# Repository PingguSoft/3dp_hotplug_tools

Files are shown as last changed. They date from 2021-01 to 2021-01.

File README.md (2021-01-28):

# [ 3dp_hotplug_tools](https://github.com/PingguSoft/3dp_hotplug_tools)

## hot-pluggable 3d printer tools
 - remixed from ProperPrinting's tools 
 - https://www.thingiverse.com/thing:3369444
 - https://www.thingiverse.com/thing:3547740
 - female connector is built in the base and male connector is built in the tools
   - **big current flows through VBB (24V for ender3) and extruder heater pins, so 4 pins for each are assigned**
   - **required voltages can be driven through VBB and GND by using DC-DC converter**
 
## base
 - female connector is installed by 15 degree angle 

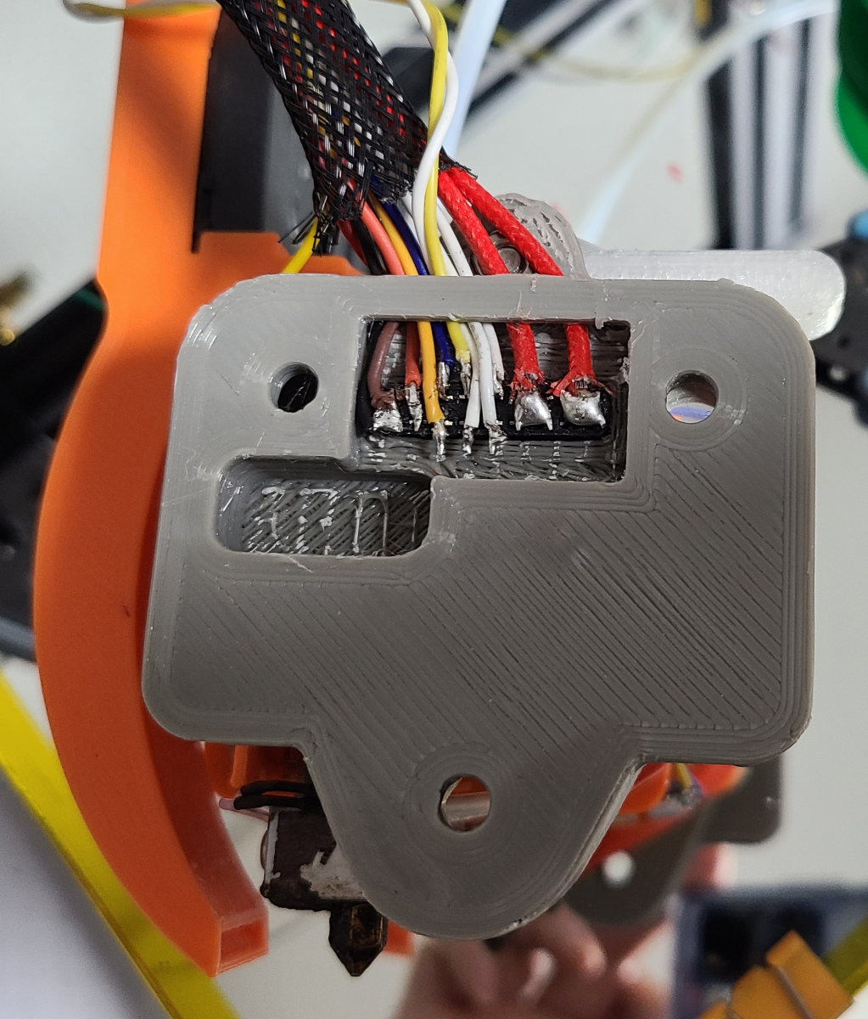
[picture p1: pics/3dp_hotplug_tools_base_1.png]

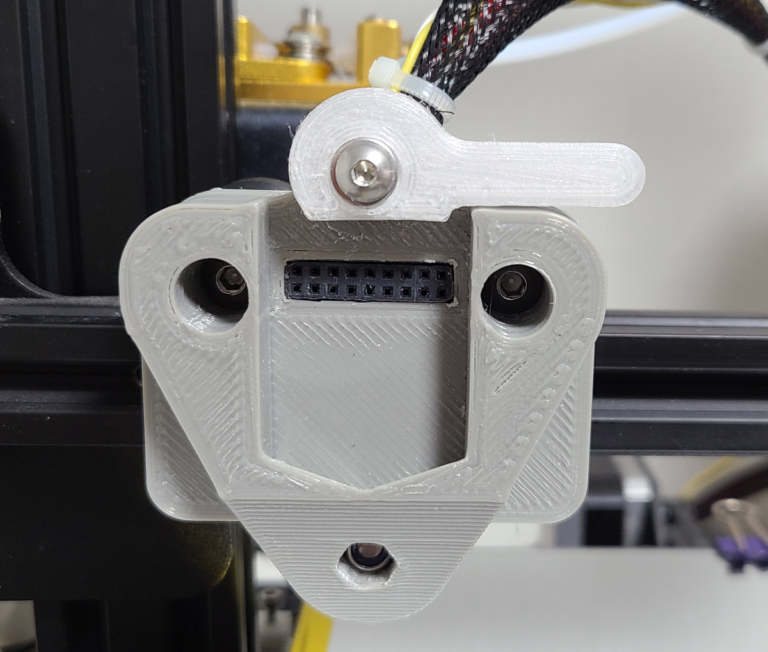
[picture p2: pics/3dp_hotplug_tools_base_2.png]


## head tool pin connection
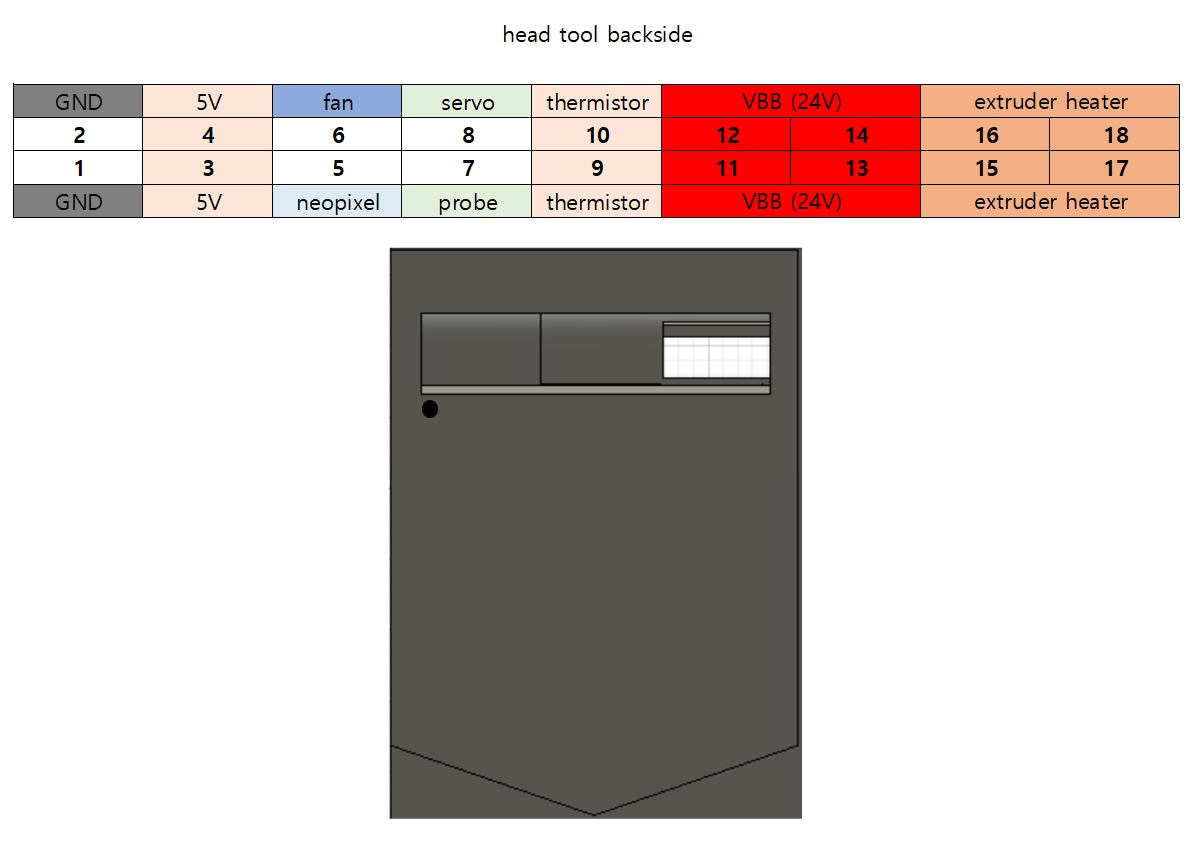
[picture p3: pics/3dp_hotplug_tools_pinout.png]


## 3dp hotend tool
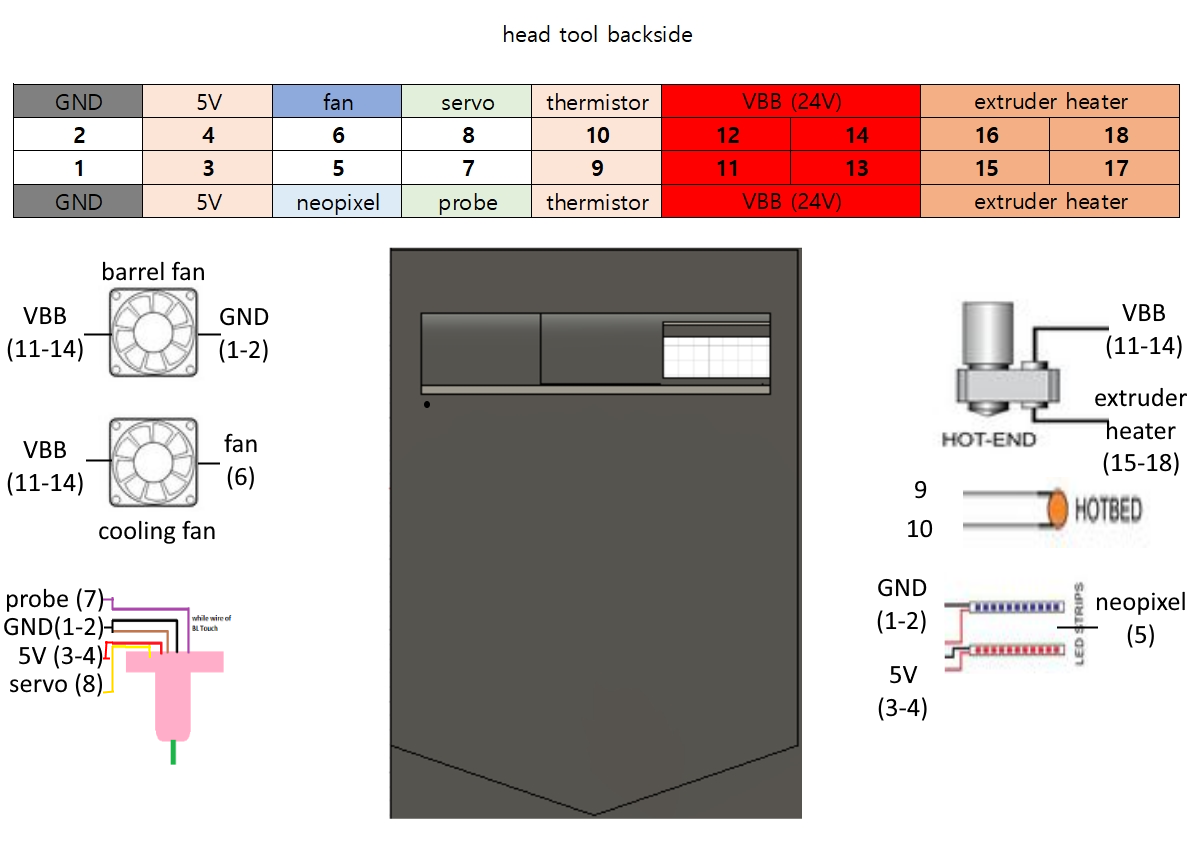
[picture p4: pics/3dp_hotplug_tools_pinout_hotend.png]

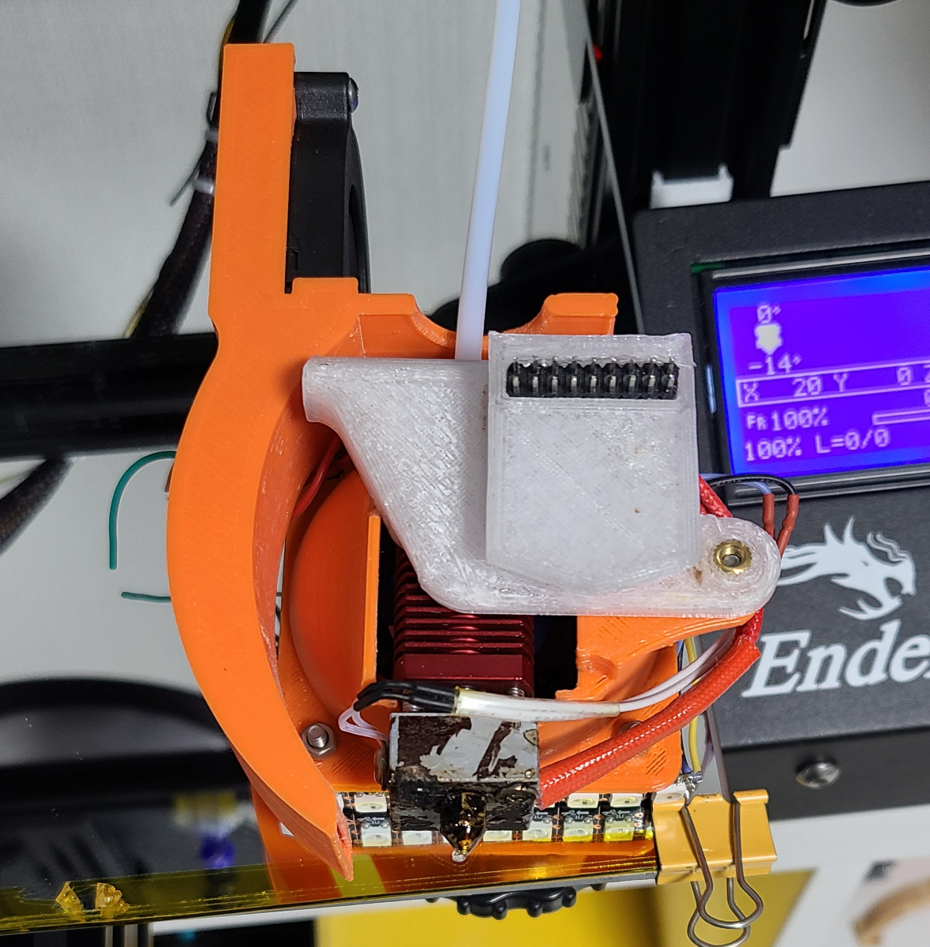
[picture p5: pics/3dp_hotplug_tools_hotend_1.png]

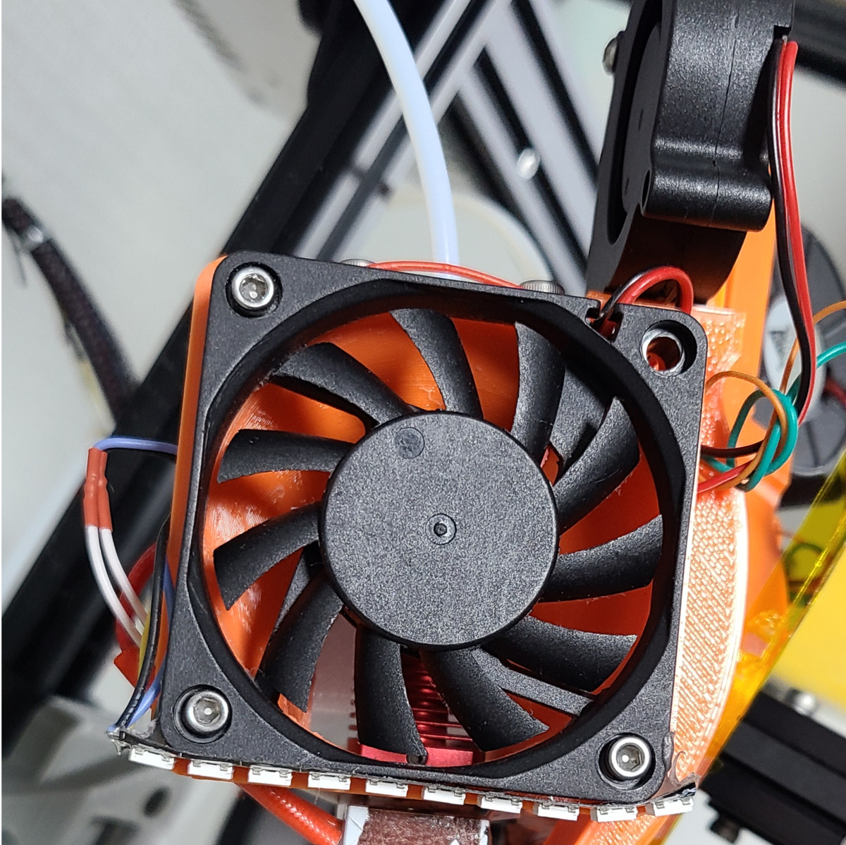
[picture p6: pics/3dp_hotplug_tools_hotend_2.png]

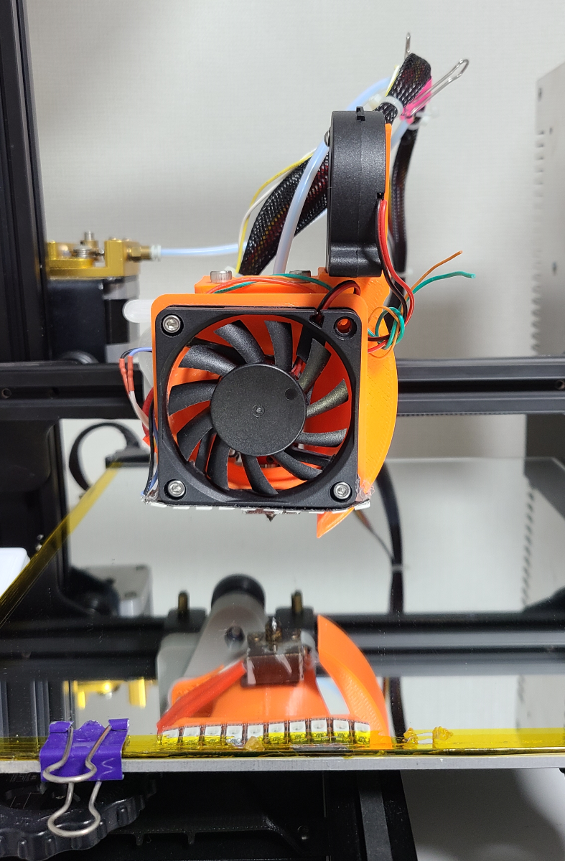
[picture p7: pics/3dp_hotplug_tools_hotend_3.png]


## plotter tool
 - pen is moved up and down by using fan signal to speed up
 - pen is moved by solenoid and gravity and move up when solenoid is on (=fan is on)
 - cura plugin for the plotter is [here](https://github.com/PingguSoft/cura_plugin)
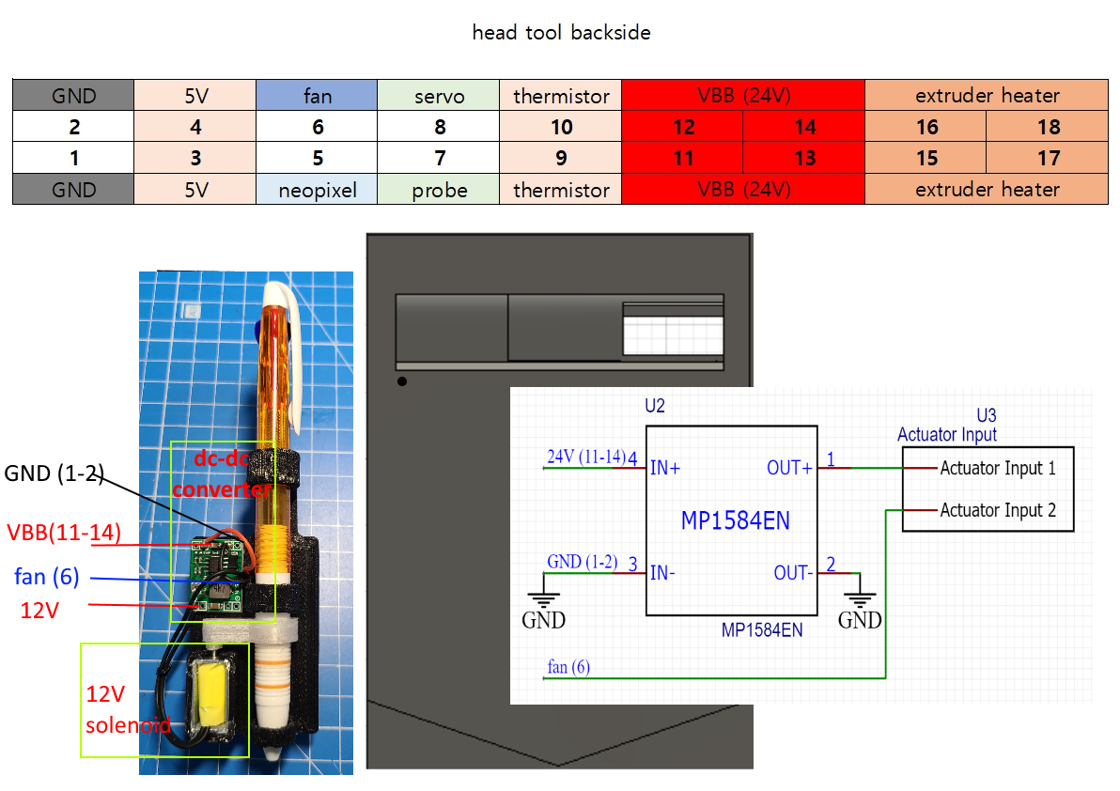
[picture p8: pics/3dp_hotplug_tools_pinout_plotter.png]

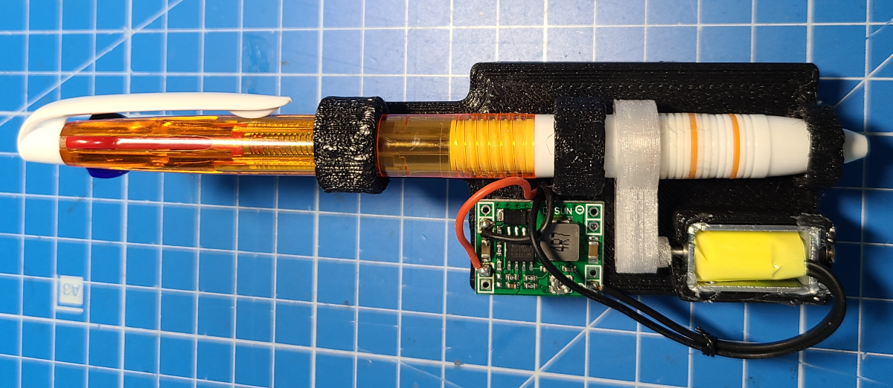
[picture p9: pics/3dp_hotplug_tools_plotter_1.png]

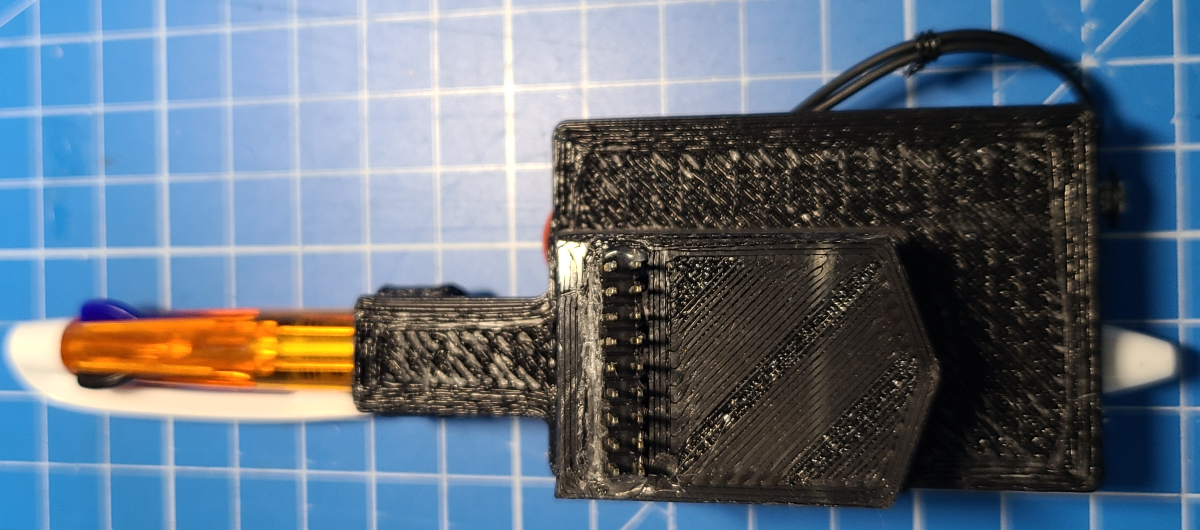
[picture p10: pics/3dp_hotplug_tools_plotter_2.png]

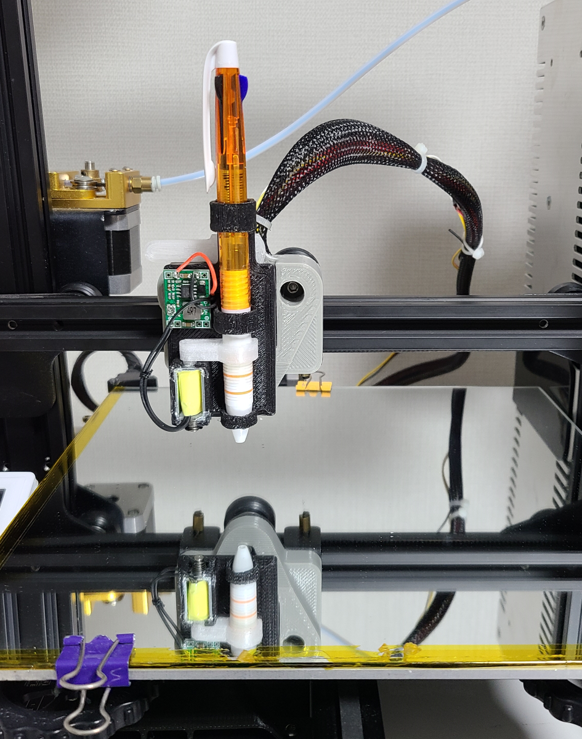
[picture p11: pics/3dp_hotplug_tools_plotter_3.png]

<div >
  <a href="https://www.youtube.com/watch?v=ooa_5NmSuvM">
</div>

## laser tool
 - laser voltage is controlled by using fan signal for laser module without pwm signal
 - if laser module has pwm signal, 15A mosfet module is not required
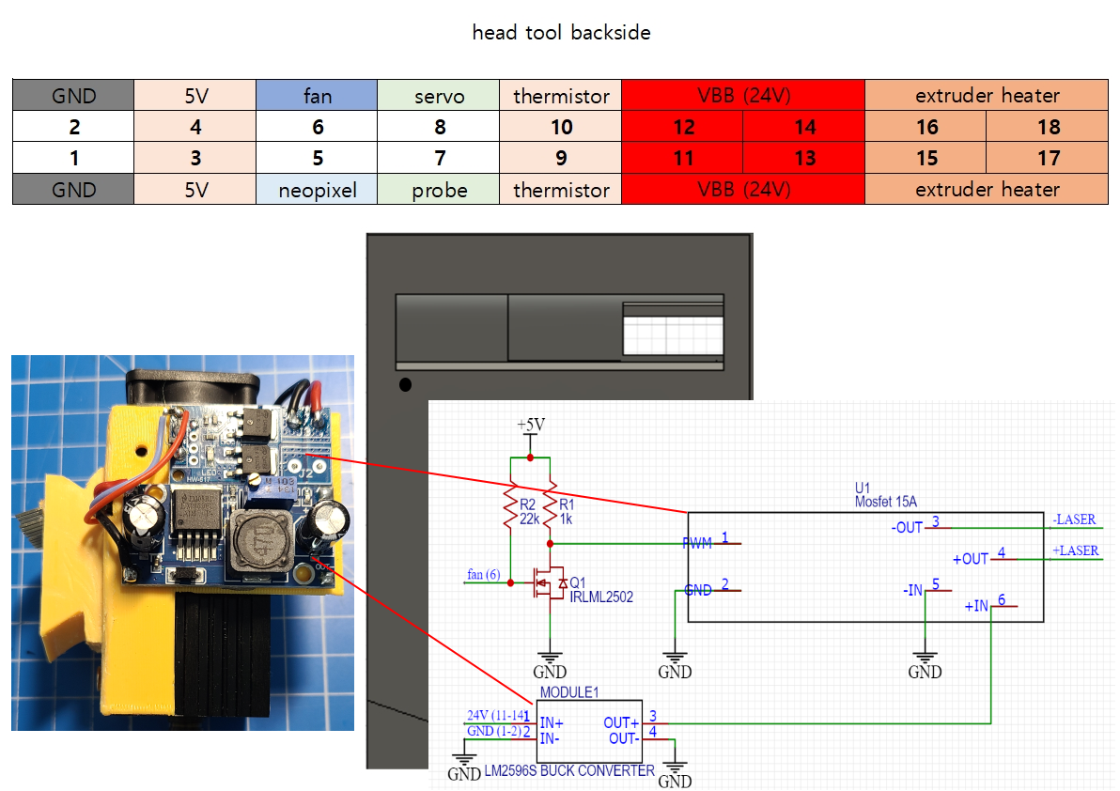
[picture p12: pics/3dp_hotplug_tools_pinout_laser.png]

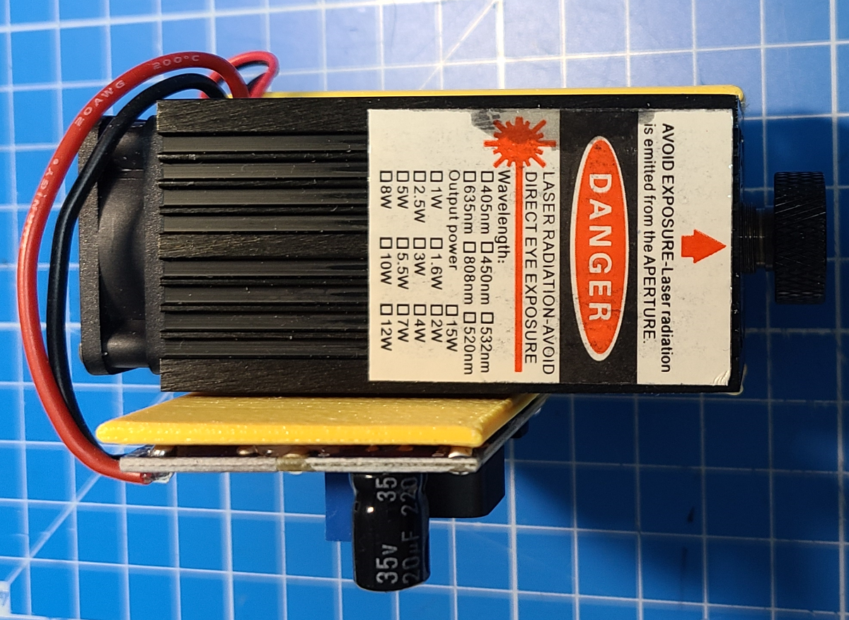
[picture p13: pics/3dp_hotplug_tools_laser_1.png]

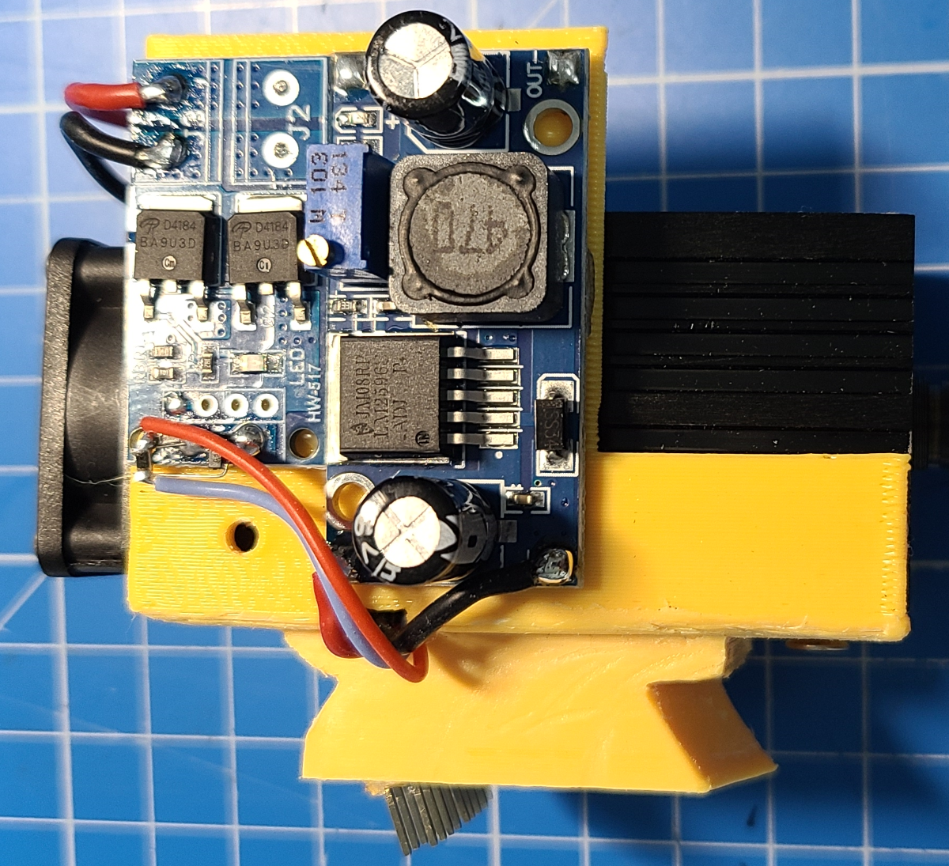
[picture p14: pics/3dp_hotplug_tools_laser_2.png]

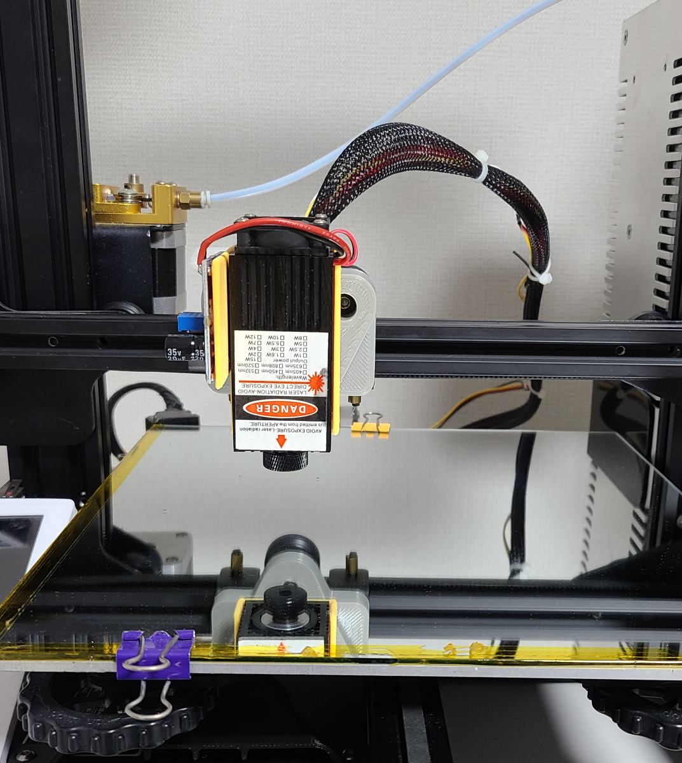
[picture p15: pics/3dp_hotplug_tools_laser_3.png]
<div>
 <a href="https://www.youtube.com/watch?v=72gGR1SVQI4">
</div>

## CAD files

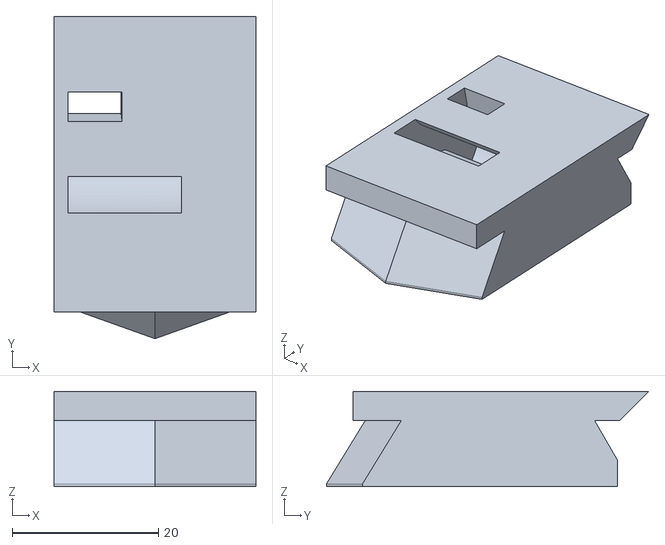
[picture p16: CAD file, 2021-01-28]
stl/06.tools-template.stl
27.6 x 44.1 x 13.0

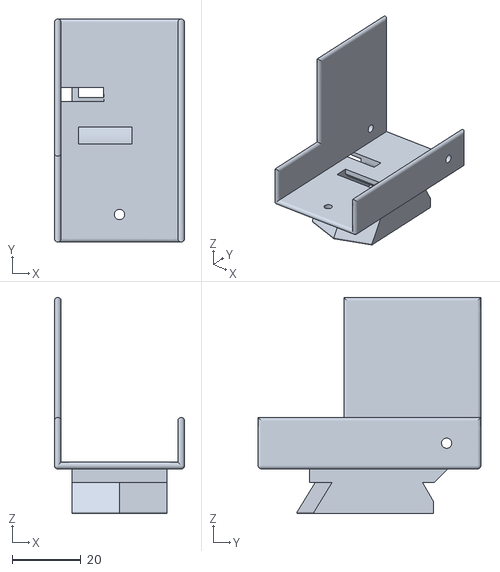
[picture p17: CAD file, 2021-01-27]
stl/05.laser.stl
38.0 x 65.0 x 63.0

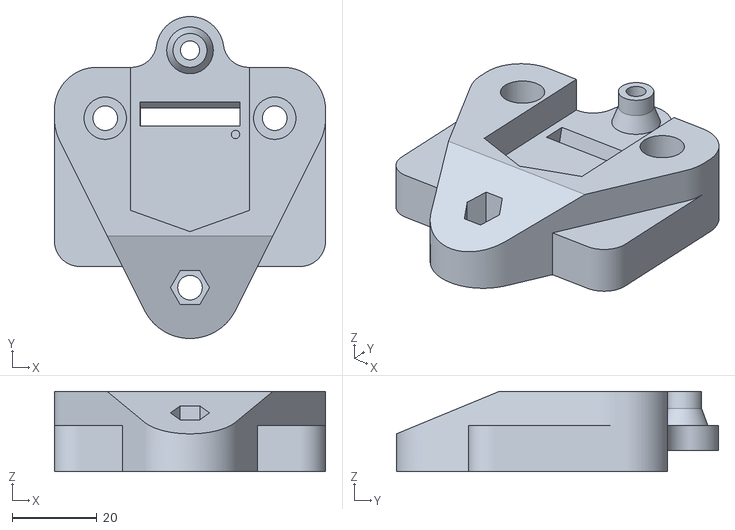
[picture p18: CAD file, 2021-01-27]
stl/01.base.stl
64.0 x 76.0 x 18.9

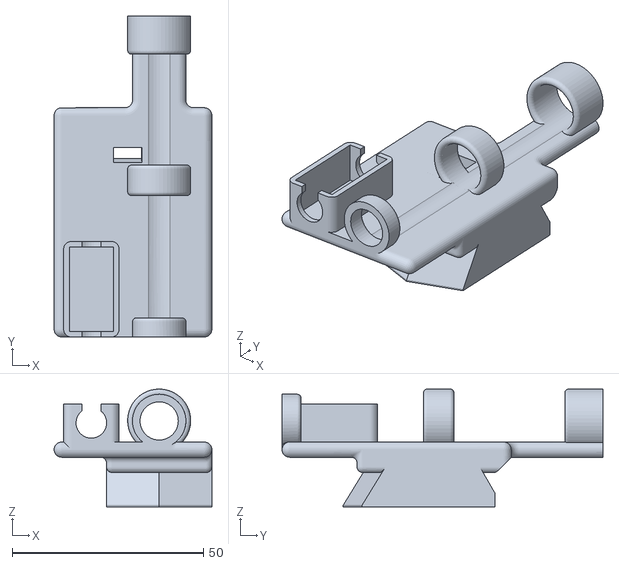
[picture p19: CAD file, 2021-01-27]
stl/03.pen_head.stl
41.3 x 84.0 x 30.9

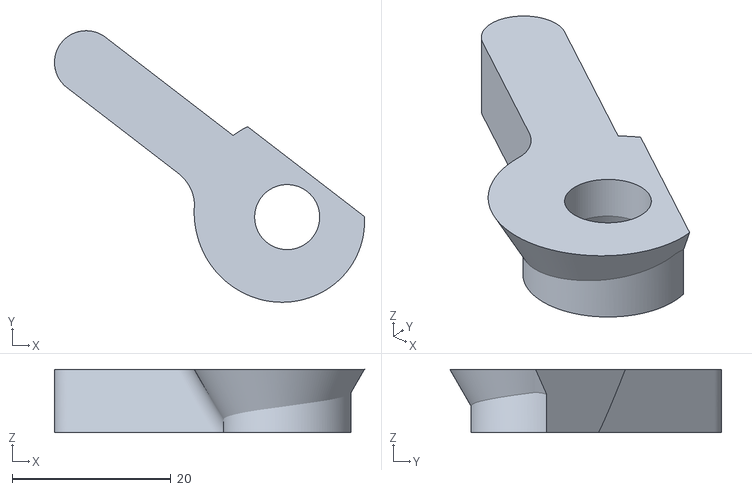
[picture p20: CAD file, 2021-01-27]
stl/06.V2_Lever.stl
39.1 x 34.3 x 8.00

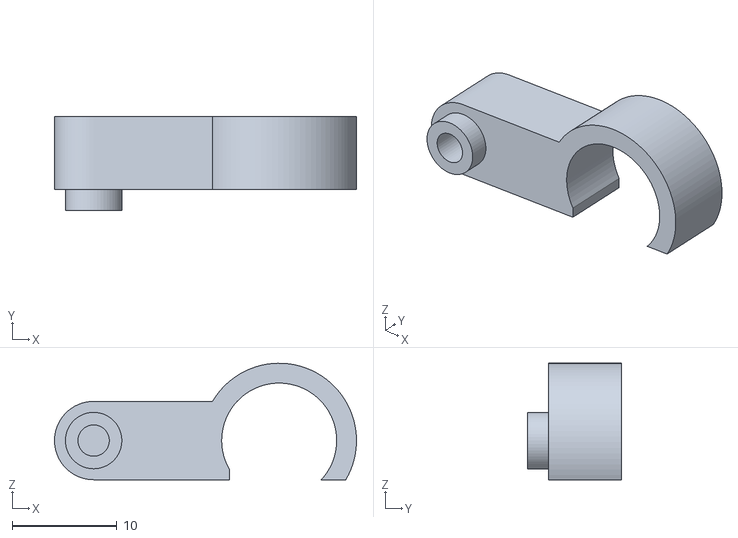
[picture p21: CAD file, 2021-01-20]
stl/04.pen_connector.stl
28.9 x 9.00 x 11.1

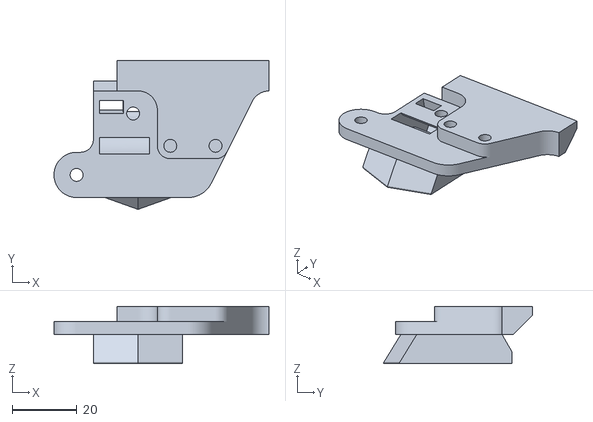
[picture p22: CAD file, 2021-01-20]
stl/02.hotend.stl
66.5 x 46.1 x 17.8

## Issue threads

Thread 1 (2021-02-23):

Plotter Pen

ckvsoft, 2021-02-23:
Hallo
Where i can get the Plotterpen or any Description how i can build the pen hardware?
thx Chris

PingguSoft, 2021-02-23:
all stl files are shared in this github.
for plotter pen, you need to print below 2 files but you need 01.base.stl and some h/w modification as I did.
- 03.pen_head.stl,
- 04.pen_connector.stl

And electronic parts are
1 solenoid https://www.aliexpress.com/item/4000067584875.html?spm=a2g0o.productlist.0.0.7ce1c629KZORd7
1 dc-dc converter for 24v printer such as Ender3, if your printer uses 12v, you don't need it.

As schematic shows,
https://raw.githubusercontent.com/PingguSoft/3dp_hotplug_tools/main/pics/3dp_hotplug_tools_pinout_plotter.png
solenoid (actuator) is controlled by cooling fan.

thx.

PingguSoft, 2021-02-23:
> Hallo
> Where i can get the Plotterpen or any Description how i can build the pen hardware?
> thx Chris

all stl files are shared in this github.
for plotter pen, you need to print below 2 files but you need 01.base.stl and some h/w modification as I did.
03.pen_head.stl,
04.pen_connector.stl

And electronic parts are
1 solenoid : https://www.aliexpress.com/item/4000067584875.html?spm=a2g0o.productlist.0.0.7ce1c629KZORd7
1 dc-dc converter for 24v printer such as Ender3, if your printer uses 12v, you don't need it.
https://www.aliexpress.com/item/32979661350.html?spm=a2g0o.productlist.0.0.5a5e7b08YzM9Fn

As schematic shows,
https://raw.githubusercontent.com/PingguSoft/3dp_hotplug_tools/main/pics/3dp_hotplug_tools_pinout_plotter.png
solenoid (actuator) is controlled by cooling fan signal.

thx.

ckvsoft, 2021-02-23:
Thank you
That I have to change the hardware is clear to me. But I thought that it must be a certain pen.
I am experimenting with a quick-change bracket with pogo pins.

thx chris

PingguSoft, 2021-02-23:
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

any pen is possible if its diameter fits the holder connector.
I think you can modify it easily if it doesn't fit.
and I also think pogo pins are very good idea

thx

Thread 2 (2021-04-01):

Connector

ckvsoft, 2021-04-01:
Hallo
Can u tell me where i can found the Connector? Is this 2mm or 2.54mm Pitch?
I search by Ali and Ama...

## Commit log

2021-01-27 laser module added
    [01.base.stl, 03.pen_head.stl, 05.laser.stl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]
2021-01-28 template added
    [06.tools-template.stl]
